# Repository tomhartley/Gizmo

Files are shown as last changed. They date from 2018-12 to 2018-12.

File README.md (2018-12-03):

# Sandala

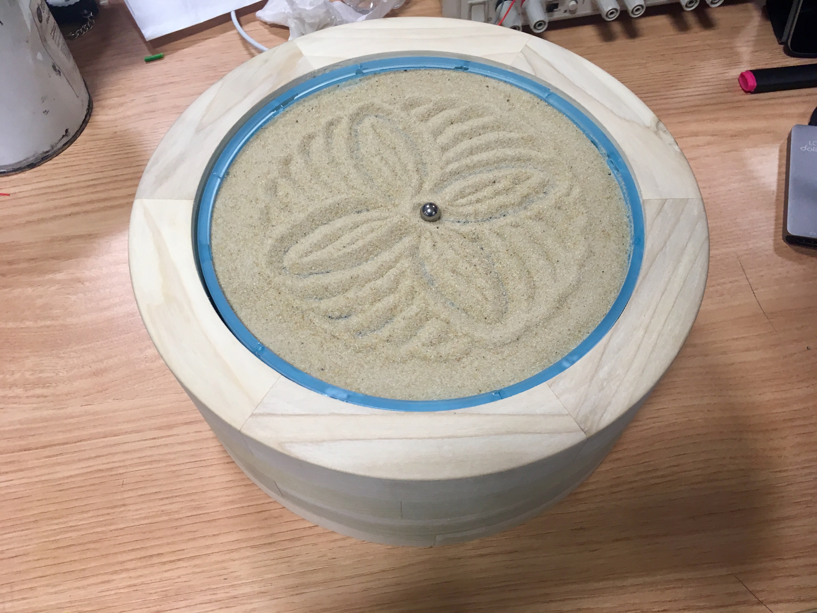
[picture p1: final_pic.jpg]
sandala-photo


Sandala is device that sketches patterns similar to those generated by a spirograph in sand. It does this by rolling a ball bearing through the sand, controlling it with a magnet from underneath.

### How does it work?

There are two stepper motors. One drives the horizontal motion of a magnet through a rack-and-pinion. The other drives the rotational movement of the plate the sand is sat upon.

### How can I build my own Sandala?

Laser cut the files (in final_to_cut.dwg) into 3mm acrylic, then glue together, ensuring all joins are at 90 degrees while they're glued. Along with the laser cut parts, you will need the following items:

- 2 NEMA 17 Stepper Motors
- 1 Sanguinololu board, or Arduino compatible board with 2 stepper drivers
- 1 Potentiometer
- 1 micro switch to act as end-stop
- 1 neodynium magnet, 3mm x 10mm
- 1 ball bearing
- Sand
- Superglue for assembly

On the linear axis, you should take the piece that moves (with the rack) and sand down the edges of each side so they're slightly chamfered. This helps this slider move more freely through the 4 supports.

### How can I make a case like the wooden one in the photo above?

You will need to have access to a lathe, and the process is relatively complex taking several days of workshop time. First, I formed 60 degree segments which were glued together in 6es to form rings. These rings were then stacked (4 high in my case), and glued together. They were then turned on a lathe to form both the inside and the outside to the correct dimensions. Sand thoroughly, then remove from the lathe and insert the acrylic structure inside.

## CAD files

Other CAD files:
Hardware/final_to_cut.dwg
Hardware/final_separate.dwg

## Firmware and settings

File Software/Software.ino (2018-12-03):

//Code to drive two stepper motors to generate sweet patterns in sand

#include <AccelStepper.h>

// defines pins numbers
const int stepPinA = 15; //A is the linear motor
const int dirPinA = 21; 

const int stepPinB = 22; //B is the radial motor
const int dirPinB = 23;

const int stopPin = 18; //The pin of the E-Stop (low-going)

//Create two steppers objects
AccelStepper linear(1, stepPinA, dirPinA);
AccelStepper circular(2, stepPinB, dirPinB);

void setup()
{
    linear.setMaxSpeed(200.0);
    linear.setAcceleration(100.0);
    
    linear.setPinsInverted(true,false,false);
    
    circular.setMaxSpeed(30000.0);
    circular.setAcceleration(1000000.0);
    circular.setSpeed(500.0);
   
    pinMode(stopPin,INPUT_PULLUP);
    homeLinear();
}

void loop()
{
    //Set the speed to the potentiometer position divided by 3 (so it's in a reasonable range)
    linear.setMaxSpeed(float(analogRead(A2))/3);
    
    if (linear.currentPosition() < 5) { //cycle in and out
      linear.moveTo(2250);
    } else if (linear.currentPosition() > 2245) {
      linear.moveTo(0);
    }
    linear.run(); //update movement of linear motor
    circular.runSpeed(); //update movement of other motor
}

void homeLinear() //This homes the linear position using the end stop, then sets the stepper so a position of 0 is in the middle 
{
    linear.moveTo(linear.currentPosition()+10000); //move further than possible.

    while (digitalRead(stopPin)!=0) {
      linear.run();
    }
    
    linear.setCurrentPosition(2300);
    linear.runToNewPosition(0); //(center)
}

void vibrate() { //Unused so far, but if this is run, it will vibrate the plate for about a minute to clear the sand.
  linear.runToNewPosition(0);
  for (int i = 0; i<350; i++) {
    circular.runToNewPosition(circular.currentPosition()+400);
    circular.runToNewPosition(circular.currentPosition()-400);
  }
  circular.setSpeed(500.0);
}
